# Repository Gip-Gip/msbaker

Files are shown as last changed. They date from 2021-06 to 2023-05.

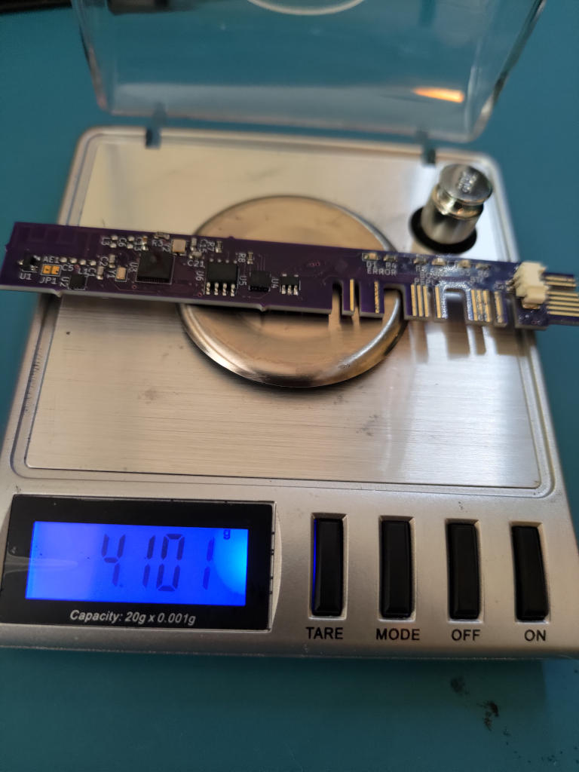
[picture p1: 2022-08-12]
docs/Images/msbaker_rev2_weight.jpg

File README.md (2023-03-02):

**Ms. Baker is a compact microcomputer built off the RP2040, specifically with model rocketry in mind.**
Occupying a footprint under 10cm&sup2;, this computer provides a unique density of many useful components, including a compact **25 pin GPIO** connector and a high accuracy **IMU**.
These features in a compact and light package is especially useful for low and medium power rockets, but may also find use in other applications where an ultra-small microcomputer may be needed.

## Feature Set

Ms. Baker is fairly feature packed for the size, and includes:

### RP2040 MCU

Powered by Raspberry Pi's RP2040 Microcontroller, Ms. Baker has the computation power of a 133MHz dual-core Arm Corted-M0+ processor in an unbelievably compact package.

### Micro SD Card Slot

Useful for logging data and loading/storing programs, Ms. Baker comes equipped with a compact MicroSD card slot for easy-to-use data storage.

### I2C IMU

No rocket computer should be complete with at least some form of telemetry, and Ms. Baker comes with the versitile LSM6DSO32 IMU, providing both gyro and acceleration data at a sample rate of up to 6.7kHz.
It has a maximum measurable acceleration range of &plusmn;32*g* and a maximum measurable angular rate of &plusmn;200dps, which should be good for most low and medium powered rockets, in theory.

### USB Programmable ROM

Thanks to the RP2040 Ms. Baker is entirely programmable via USB, meaning so long as you have a Micro USB cable and a computer you have access to **16MBytes of ROM** with no extra hardware!

### GPIO

Utilizing a Molex SlimStack connector Ms. Baker provides 25 pins of GPIO in a very compact footprint, completely up for any use the end user may desire!

### Robust Firmware

Like any other OpenApeShop project, Ms Baker's firmware is *(to be written)* in the Rust programming language, making it very robust and resistant to common bugs that may occur in other embedded firmware solutions.

## Development Status

**With a working prototype**, Ms. Baker is on it's third prototype and has the following steps that need to be completed before it is more or less ready for use:

- [ ] Program the firmware so that by default Ms. Baker acts as a telemetry logging device
- [ ] Field test Ms. Baker on a live rocket
- [ ] Reorganize PCB to fill up any unused space by
    - [ ] Spacing traces to reduce the chances of crosstalk, when possible
    - [ ] Increasing the size of traces to reduce impedence, when possible
- [ ] Document Ms. Baker so it's easy to use
- [ ] Develop a pin breakout board so prototyping is as easy as with a normal Raspberry Pi Pico

## Legal

Ms Baker's hardware is under the CERN-OHL-S and software under GPL-3.0.
See LEGAL-HARDWARE for all legal info regarding hardware, LEGAL-SOFTWARE for all legal info regarding software.

## Links

* [Website](https://openapeshop.org/hardware/msbaker)
* [Schematic](https://github.com/Gip-Gip/msbaker/raw/main/docs/Renders/schematic.png)

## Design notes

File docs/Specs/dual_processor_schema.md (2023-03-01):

---
title: "Dual Processor Schema"
date: 2023-03-01
author:
    - Charles Thompson
tags:
    - Specifications
    - Software
---
In embedded systems it is important that everything run efficiently as possible, and since the RP2040 is a dual core processor it would be a waste to not utilize both cores to their full potential. Therefore it is important to outline what responsibilities each core does so that programming for the processor is straightforward and well defined.

## Processor Responsibilities
Ms. Baker is to use a In-Out dual processor schema, in that one processor gathers input data and the other writes output data. The individual responsibilities are as follows:

### Core 0(In):
1. Initialize everything
2. Keep track of time
3. Read sensors on a consistent basis(be on time)
4. Handle aborts
5. Send data to core 0 to be processed, with high and low priority

### Core 1(Out):
1. Perform tasks assigned by core 0, high priority first, pertaining to
    * Computing and storing telemetry of the computer
    * Adjusting flight path and moving actuators when hooked up to external gear
    * Writing telemetry to the SD card

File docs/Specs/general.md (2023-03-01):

---
title: "General Specifications"
date: 2022-08-19
author:
    - Charles Thompson
tags:
    - Specifications
    - General
    - Overview
    - Hardware
    - Software
---
# General Specifications of the Ms. Baker Microcomputer
## The Need for a Compact Microcomputer in Rocketry

With modern advancements in chip design decreasing footprint and increasing computation power and effeciency, along with the shrinkage of many passive components, it is more than possible to cram fully capable flight computation units along with basic telemetry in a sub 10cm² package. The benefits for this are several, including but not limited to weight savings, dev time savings(not needing to design a custom computer for a project), and cost savings. This improvements are of both a combination of modern technology and advanced board design which is all open sourced and openly developed to help lead to future improvements in the unexplored tech. On top of that, these improvements are all fairly substantial to hobby model rocketry as every little change especially counts at the small rocket scale.

**Weight savings** is the primary benefit of the Ms. Baker microcomputer. The second iteration of the microcomputer only weighed in at **4g** in total, which is only really comparible to basic barometer altimeters and blows any proper flight computer out of the water[1]. Less weight leads to a higher acceleration under the same force, and consequentially a higher apogee aswell [2]. These weight savings are very significant as they can result in a multi-percent decrease in the total mass of a common 100-300g rocket[3]. For example, you replace a 15g flight computer on an 100g rocket(with a gross weight of 115g) with Ms. Baker which comes in at 4g(a new gross weight of 104g), you get a weight reduction of 9.6%, which is not insubstantial by any means.

**Development time** is saved by making Ms. Baker versitile and GPIO-ready. Most model rocket altimeters and flight computers are either massive and expensive, or have little to no expandable GPIO[1]. Ms. Baker aims to fill a niche by providing **I2C GPIO** to the end user so they can implement pyro controls, flight controls, and etc. themselves without having to worry about developing the complex circuitry to support a **full 32-bit microcontroller**. This also allows for **easier and more robust programming** as even simple solutions can utilize a 32-bit ARM core to speed up and improve accuracy for any need that may be. Even larger projects can utilize Ms. Baker as the brains for their custom boards as it's small footprint allows for more space for power electronics and other chips & sensors that may be needed.

**Cost Savings** *todo*

## What is Required for Ms. Baker to Meet It's Goals?

Ms. Baker has a lot of things it needs to fullfill, and each requirement brings it twords the goal of it being a fully fledged microcomputer

 * A **RP2004** MCU at the heart of the project. The RP2040 is low cost and OSH-friendly, with an open-source bootROM and good support for Rust
 * Firmware programmed in **Rust**. Rust is a powerful language that enforces good programming habits and allows the firmware to be far more robust by nature than if it were built in another language such as C or C++
 * On-board **accelerometer** and **gyroscope**, ideally in the same chip as this allows Ms. Baker to keep approximate relative location of the microcomputer
 * **10 meter** apogee accuracy when measuring apogee, under 10000 meters
 * Robust **GPIO** connectors and/or headers for expanding the use of the computer into other projects, with a minimum of one **I2C** interface
 * **USB** interface for extracting data from previous flights *and* programming the computer
 * **4MB** flash storage for plenty of room to program
 * **F-RAM** for storing non-volitile flight telemetry data
 * Total area under **10cm²**, and ideally small enough to fit into an estes gnome

## Finding Telemetric Accuracy
### Calculating Distance from Rocket Acceleration

First you need to find the initial hypothetical apogee from a hypothetical rocket's acceleration. Let's say the rocket accelerates at around 16g for 1 second, the rocket would gain $s_1$ distance and $v_1$ velocity by the time the rocket looses power
  $$
  \begin{aligned}
  &v = u + at\\
  &v = 0 + 156.9_{m/s^2}\cdot1_s\\
  \\
  &v_1 = 156.9_{m/s}
  \end{aligned}
 $$
$$
\begin{aligned}
\\
&v^2=u^2+2as\\
&2as=v^2-u^2\\
&s_1=\frac{v_1^2-u^2}{2a}\\
\\
&s_1=\frac{156.9_{m/s}^2-0_{m/s}^2}{2\cdot156.9_{m/s^2}}
\\
&s_1=78.5_m
\end{aligned}
$$
Then from there you can find the distance($s_2$) it takes the rocket to reach it's apogee
$$
\begin{aligned}
&u_2=v_1\\
\\
&s_2=\frac{v_2^2-u_2^2}{2a_2}\\
\\
&s_2=\frac{0_{m/s}^2-156.9_{m/s}^2}{2\cdot-9.8_{m/s^2}}
\\
&s_2=1256_m
\end{aligned}
$$
After that, you can find the total distance($s_t$) by adding $s_1$ and $s_2$, in this case $s_t=s_1+s_2=1334.5_m$. To condense the steps needed to get $s_t$, we can simply concatenate the above math into one equation
$$
\begin{aligned}
&s_t = s_1 + s_2\\
&s_t = \frac{v_1^2}{2a}+\frac{-v_1^2}{2\cdot-9.8_{m/s^2}}\\
\\
&s_t = \frac{(at)^2}{2a}+\frac{(at)^2}{19.6_{m/s^2}}
\end{aligned}
$$

## Part Selection

 * MPU: **RP2040**
     * Open-Source boot rom
     * Flash-able without any extra hardware via USB
     * Micro-SD card support
     * 2 i2c interfaces, 2spi interfaces
     * Up to 16mb external programmable flash
 * IMU: **LSM6DSO32TR**
 * Flash: **W25Q128JVSIM TR**
     * Reccomended flash for the RP2040
     * 16mb fast program storage
 * Voltage Regulator: **MIC5365-3.3YC5-TR**
 * Micro-USB port: **105017-0001**
 * MicroSD card connector: **104031-0811**
 * GPIO connector: **5055513420**
 * Crystal: **445I23D12M00000**

# Citations

 1. “Model Rocket Altimeters: Comparison Guide,” *Model rocket altimeters: Comparison guide*. \[Online\]. Available: [http://rocketsetc.com/altimeter-comparison/](http://rocketsetc.com/altimeter-comparison/). \[Accessed: 12-Aug-2022\].
 2. T. Benson, “Acceleration during powered flight,” *NASA*, 15-Aug-1999. \[Online\]. Available: [https://www.grc.nasa.gov/www/k-12/VirtualAero/BottleRocket/airplane/rktapow.html](https://www.grc.nasa.gov/www/k-12/VirtualAero/BottleRocket/airplane/rktapow.html). \[Accessed: 12-Aug-2022\].
 3. “HB:modelrockets,” *LUNAR*. \[Online\]. Available: [http://www.lunar.org/wiki/tiki-index.php?page=HB%3AModelRockets](http://www.lunar.org/wiki/tiki-index.php?page=HB%3AModelRockets). \[Accessed: 12-Aug-2022\].

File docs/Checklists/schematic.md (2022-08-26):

---
title: "Schematic Checklist"
date: 2022-08-26
author:
    - Charles Thompson
tags:
    - Checklist
    - General
    - Hardware
---
# RP2040 Checklist
### Derived from [Hardware design with RP2040](https://datasheets.raspberrypi.com/rp2040/hardware-design-with-rp2040.pdf) and the RP2040 [Datasheet](https://datasheets.raspberrypi.com/rp2040/rp2040-datasheet.pdf)
 - [ ] Power
     - [ ] 3.3v LDO Voltage Regulator
     - [ ] Decoupling capacitors
         - [ ] 100n capacitors on pins 49, 42, 33, 22, 10, 1, 48 and 43
         - [ ] 100n capacitors on pins 50 and 23
         - [ ] 1u capacitors on pins 45 and 44
 - [ ] Flash Storage
     - [ ] W25Q128JVS flash chip
 - [ ] Crystal Oscillator
     - [ ] 33p capacitor connected to each pin on the crystal
     - [ ] 1k resister in series between the crystal and XOUT
     - [ ] Crystal with ESR of 50ohms and 18p load capacitance
 - [ ] I/O
     - [ ] USB
         - [ ] 27.4ohm resistor in series with USB_D+ and USB_D-
     - [ ] GPIO
         - [ ] All GPIO pins availible to the GPIO header, excluding GPIOs used for the SD card
         - [ ] Run, SWD, and SWCLK also availible to the GPIO header
     - [ ] I2C
         - [ ] Pullup resistors correct value
         - [ ] All ICs connected to I2C0 on pins 8 and 9
             - [ ] SDA on pin 8
             - [ ] SCL on pin 9
     - [ ] SD Card
         - [ ] 10u decoupling capacitor between VDD and ground
         - [ ] All data lines contiguous and in order
     - [ ] Green Status LED
         - [ ] 470 ohm current limiting resistor
     - [ ] Reset Header
         - [ ] Connected to the RUN pin
     - [ ] Bootsel Jumper
         - [ ] Connected to QSPI_SS
         - [ ] 1k resistor between jumper and ground
     - [ ] Test Pads
         - [ ] 3.3v test pad
         - [ ] 1.1v test pad
         - [ ] XIN test pad
         - [ ] I2C SDA test pad
         - [ ] I2C SCL test pad

# LSM6DSO32 Checklist
### Derived from [iNEMO inertial module: always-on 3D Accelerometer and 3D gyroscope](https://www.st.com/resource/en/datasheet/lsm6dso32.pdf)
 - [ ] Power
     - [ ] 3.3v supply connected to pins 8 and 5
     - [ ] 100n capacitors connected to pins 8 and 5
     - [ ] Ground connected to pins 6 and 7
 - [ ] I2C
     - [ ] SA0(pin 1) connected to ground to set the I2C lsbit to zero
     - [ ] SDx and SCx connected to ground
     - [ ] INT1 not connected
     - [ ] INT2 not connected
     - [ ] CS connected to 3.3v
     - [ ] SCL connected to I2C0_SCL
     - [ ] SDA connected to I2C0_SDA

# W25Q128JVSIM Checklist
### Derived from the W25Q128JV [Datasheet](https://www.winbond.com/hq/support/documentation/downloadV2022.jsp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) and [Hardware design with RP2040](https://datasheets.raspberrypi.com/rp2040/hardware-design-with-rp2040.pdf)
 - [ ] Power
     - [ ] 3.3v supply connected to pin 8
     - [ ] 100n capacitor connected to pin 8
     - [ ] Ground connected to pin 4
 - [ ] QSPI
     - [ ] QSPI_SS connected to CS
     - [ ] QSPI_SCLK connected to CLK
     - [ ] QSPI_SD0-3 connected to IO0-3

# MIC5365-3.3YC5 Checklist
### Derived from the MIC5465 [Datasheet](https://ww1.microchip.com/downloads/aemDocuments/documents/OTH/ProductDocuments/DataSheets/mic5365.pdf)
 - [ ] Power
     - [ ] 1u capacitor connected to both pins 1 and 5
     - [ ] VIN connected to +5v rail
     - [ ] VOUT connected to +3.3v rail
 - [ ] EN pin connected to +5v

# Final Checklist
 - [ ] RP2040 Checklist Complete
 - [ ] LSM6DSO32 Checklist Complete
 - [ ] W25Q128JVSIM Checklist Complete
 - [ ] MIC5365-3.3YC5 Checklist Complete
 - [ ] No unconnected pins or nets
 - [ ] ERC ran
 - [ ] Schematic organized
 - [ ] BOM generated
 - [ ] Footprints set
 - [ ] MPNs set

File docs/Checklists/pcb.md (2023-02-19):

---
title: "PCB Checklist"
date: 2022-08-26
author:
    - Charles Thompson
tags:
    - Checklist
    - General
    - Hardware
---
# RP2040 Checklist
### Derived from [Hardware design with RP2040](https://datasheets.raspberrypi.com/rp2040/hardware-design-with-rp2040.pdf) and the RP2040 [Datasheet](https://datasheets.raspberrypi.com/rp2040/rp2040-datasheet.pdf)
 - [ ] Power
     - [ ] Decoupling capacitors close to pins
 - [ ] Crystal Oscillator
     - [ ] Close to RP2040 to reduce parasitic capacitance
     - [ ] Capacitors and resistor close to crystal
 - [ ] Flash
     - [ ] Data lines short and close to the RP2040
 - [ ] I/O
     - [ ] USB
         - [ ] 0.8mm wide tracks spaced 0.15mm apart from R5 and R6

# LSM6DSO32 Checklist
### Derived from [iNEMO inertial module: always-on 3D Accelerometer and 3D gyroscope](https://www.st.com/resource/en/datasheet/lsm6dso32.pdf)
 - [ ] Power
     - [ ] Decoupling capacitors close to pins

# W25Q128JVSIM Checklist
### Derived from the W25Q128JV [Datasheet](https://www.winbond.com/hq/support/documentation/downloadV2022.jsp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) and [Hardware design with RP2040](https://datasheets.raspberrypi.com/rp2040/hardware-design-with-rp2040.pdf)
 - [ ] Power
     - [ ] Decoupling capacitors close to pins

# MIC5365-3.3YC5 Checklist
### Derived from the MIC5465 [Datasheet](https://ww1.microchip.com/downloads/aemDocuments/documents/OTH/ProductDocuments/DataSheets/mic5365.pdf)
 - [ ] Power
     - [ ] Decoupling capacitors close to pins

# Final Checklist
 - [ ] RP2040 Checklist Complete
 - [ ] LSM6DSO32 Checklist Complete
 - [ ] W25Q128JVSIM Checklist Complete
 - [ ] MIC5365-3.3YC5 Checklist Complete
 - [ ] No unconnected pins or nets
 - [ ] DRC ran

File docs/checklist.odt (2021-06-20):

Ms. Baker Schematic Checklist

Schematic Revision 2.3

Write component ids under the bullet point, if applicable

# ESP32 BLOCK

- 100nF capacitors connecting esp32/pins 19 and 37 respectively to ground
- esp32/pins 19 and 37 connected to V3.3+
- 1uF capacitor connecting esp32/pin 26 to ground
- 100nF, 1uF, and 10uF capacitors connecting both esp32/pins 3 and 4 to ground
- 2nH inductor connecting both esp32/pins 3 and 4 to the aformentioned bypass capacitors
- both esp32/pins 3 and 4 connected to V3.3+
- 100pF and 1uF capacitors connecting both esp32/pins 46 and 43 to ground
- both esp32/pins 46 and 43 connected to V3.3+
- 100nF capacitor connecting esp32/pin 1 to ground
- esp32/pin 1 connected to V3.3+
- esp32/pin 9 connected to reset
- 10nF capacitor connecting esp32/pin48 to ground
- 499ohm resistor connecting esp32/pin 41 to UART_TX
- esp32/pin 25 connected to SPI_CS
- esp32/pin 27 connected to SPI_IO1
- esp32/pin 30 connected to SPI_IO3
- esp32/pin 31 connected to SPI_CLK
- esp32/pin 32 connected to SPI_IO2
- esp32/pin 33 connected to SPI_IO0
- esp32/pin 14 connected to I2C_SCK
- esp32/pin 15 connected to I2C_SDA
- esp32/pin 23 connected to BOOTMODE
- esp32/pin 40 connected to UART_RX
- esp32/pin 34 connected to the BT STATUS LED
- esp32/pin 35 connected to the BOOT STATUS LED
- esp32/pin 36 connected to the ERROR LED
- esp32/pin 17 connected to JTAG_MTMS
- esp32/pin 18 connected to JTAG_MTDI
- esp32/pin 20 connected to JTAG_MTCK
- esp32/pin 21 connected to JTAG_MTDO

# CPU CRYSTAL BLOCK

- 40MHz crystal connected between esp32/pins 44 and 45
- 0ohm resistor in series between esp32/pin 45 and the 40MHz crystal
- 12pF capacitors connected to both 40MHz/pins 1 and 3 respectively
- 40MHz/pins 2 and 4 connected to ground

# RTC CRYSTAL BLOCK

- 32.768kHz crystal connected between esp32/pins 12 and 13
- 12pF capacitors connected to both 32.768kHz/pins 1 and 2 respectively

# RESET BLOCK

- 100nF capacitor connecting mcp130/pin 2 to ground
- jumper connecting mcp130/pin1 to reset
- mcp130/pin 2 connected to V3.3+
- mcp130/pin 3 connected to ground

# ANTENNA BLOCK

- One inductor and two capacitors configured in pi-style matching network
- Use center-tapped inductor or two inductors for tuning

# I2C PULLUP BLOCK

- 2 12kOhm resistors connecting I2C_SCK and I2C_SDA respectively to V3.3+

# LED BLOCK

- 120Ohm resistor between each LED and their respective esp32 pin
- 2.1v LEDs
- BLUE=BLUETOOTH, GREEN=STATUS, RED=ERROR

# POWER SUPPLY BLOCK

- 10uF capacitor connecting adp124/pins 7 and 8 to ground
- 10uF capacitor connecting adp124/pins 1 and 2 to ground
- 1uF capacitor connecting adp150/pin 1 to ground
- 1uF capacitor connecting adp150/pin 5 to ground
- adp124/pins 5, 7 and 8 connected to a 3.7v LiPo battery, preferably via a Molex Picoblade
- adp124/pins 1, 2, and 3 connected to V3.3+
- adp124/pin 4 connected to ground
- adp150/pins 1 and 3 connected to V3.3+
- adp150/pin 2 connected to ground
- adp150/pin 5 connected to V1.8+

# IMU BLOCK

- 100nF and 2.2uF capacitor connecting icm20601/pin 16 to ground
- 10nF capacitor connecting icm20601/pin 1 to ground
- 470nF capacitor connecting icm20601/pin 14 to ground
- icm20601/pin 1 connected to V3.3+
- icm20601/pin 2 connected to I2C_SCK
- icm20601/pin 3 connected to I2C_SDA
- icm20601/pin 4 connected to ground
- icm20601/pin 5 connected to V3.3+
- icm20601/pin 8 connected to ground
- icm20601/pin 13 connected to ground
- icm20601/pin 16 connected to V1.8V+

# FERAM BLOCK

- 2.2uF capacitor connecting fm24v01/pin 8 to ground
- fm24v01/pins 1, 2, and 3 connected to ground
- fm24v01/pin 4 connected to ground
- fm24v01/pin 5 connected to I2C_SDA
- fm24v01/pin 6 connected to I2C_SCK
- fm24v01/pin 7 connected to ground
- fm24v01/pin 8 connected to V3.3+

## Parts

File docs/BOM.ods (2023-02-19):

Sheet: product
References | Value | Footprint | Cost | MPN | Quantity | Supplier | Total Cost
C2 | 10u | Capacitor_SMD:C_0603_1608Metric | 0.38 | C1608X5R0J106K080AE | 1 | Digi-Key | 0.38
C1, C3, C7, C20 | 1u | Capacitor_SMD:C_0402_1005Metric | 0.19 | C1005X5R1E105K050BE | 4 | Digi-Key | 0.76
C4, C5 | 33p | Capacitor_SMD:C_0402_1005Metric | 0.1 | CGA2B2C0G1H330J050BA | 2 | Digi-Key | 0.2
C6, C8-C19 | 100n | Capacitor_SMD:C_0402_1005Metric | 0.2 | C1005X7R1H104K050BE | 13 | Digi-Key | 2.6
D1 | 2.1v | LED_SMD:LED_0402_1005Metric | 0.38 | APHHS1005CGCK | 1 | Digi-Key | 0.38
J1 | USB_B_Micro | Connector_USB:USB_Micro-B_Molex-105017-0001 | 0.96 | 105017-0001 | 1 | Digi-Key | 0.96
J2 | Micro_SD_Card | Connector_Card:microSD_HC_Molex_104031-0811 | 2.22 | 104031-0811 | 1 | Digi-Key | 2.22
J3 | GPIO | msbaker:5055513420 | 1.57 | 505551-3420 | 1 | Digi-Key | 1.57
JP1, JP2 | BOOTSEL, RESET | Connector_PinHeader_2.54mm:PinHeader_1x02_P2.54mm_Vertical |  |  | 2 | Digi-Key
R1, R2 | 15k | Resistor_SMD:R_0402_1005Metric | 0.1 | AC0402FR-0715KL | 2 | Digi-Key | 0.2
R3, R4 | 1k | Resistor_SMD:R_0402_1005Metric | 0.1 | AC0402FR-071KL | 2 | Digi-Key | 0.2
R5, R6 | 27.4 | Resistor_SMD:R_0402_1005Metric | 0.1 | AC0402FR-0727R4L | 2 | Digi-Key | 0.2
R7 | 470 | Resistor_SMD:R_0402_1005Metric | 0.1 | AC0402FR-07470RL | 1 | Digi-Key | 0.1
U1 | MIC5365-3.3YC5 | Package_TO_SOT_SMD:SOT-353_SC-70-5 | 0.19 | MIC5365-3.3YC5-TR | 1 | Digi-Key | 0.19
U2 | W25Q128JVS | Package_SO:SOIC-8_5.23x5.23mm_P1.27mm | 1.95 | W25Q128JVSIM TR | 1 | Digi-Key | 1.95
U3 | RP2040 | RP2040_minimal:RP2040-QFN-56 | 1 | RP2040TR13 | 1 | Digi-Key | 1
U4 | LSM6DSO32 | Package_LGA:LGA-14_3x2.5mm_P0.5mm_LayoutBorder3x4y | 5.47 | LSM6DSO32TR | 1 | Digi-Key | 5.47
Y1 | 12MHz | Crystal:Crystal_SMD_5032-2Pin_5.0x3.2mm | 0.76 | 445I23D12M00000 | 1 | Digi-Key | 0.76
PCB | 4 Layer | - | 4.47 | - | 1 | OSH Park | 4.47
 |  |  |  |  |  |  | Cost per unit
 |  |  |  |  |  |  | 23.61

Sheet: operations
Description | Cost | MPN | Quantity | Supplier | Total Cost
Stencils | 24.7 | - | 1 | OSH Stencis | 24.7

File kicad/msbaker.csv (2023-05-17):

Source: | /home/thompsonc/Projects/msbaker/kicad/msbaker.kicad_sch
Date: | Wed 17 May 2023 01:07:28 PM EDT
Tool: | Eeschema 7.0.1
Generator: | /usr/share/kicad/plugins/bom_csv_grouped_by_value.py
Component Count: | 39
Collated Components:
Item | Qty | Reference(s) | Value | LibPart | Footprint | Datasheet | DNP | Cost | MPN | Note
1 | 2 | C1, C3 | 1u | Device:C | Capacitor_SMD:C_0402_1005Metric | ~ |  | 0.19 | C1005X5R1E105K050BE
2 | 2 | C2, C21 | 4.7u | Device:C | Capacitor_SMD:C_0402_1005Metric | ~ |  | 0.53 | C1005X5R1A475K050BE
3 | 2 | C4, C5 | 33p | Device:C_Small | Capacitor_SMD:C_0402_1005Metric | ~ |  | 0.1 | CGA2B2C0G1H330J050BA
4 | 13 | C6, C8, C9, C10, C11, C12, C13, C14, C15, C16, C17, C18, C19 | 100n | Device:C_Small | Capacitor_SMD:C_0402_1005Metric | ~ |  | 0.2 | C1005X7R1H104K050BE
5 | 2 | C7, C20 | 1u | Device:C_Small | Capacitor_SMD:C_0402_1005Metric | ~ |  | 0.19 | C1005X5R1E105K050BE
6 | 1 | D1 | 2.1v | Device:LED | LED_SMD:LED_0402_1005Metric | ~ |  | 0.37 | APHHS1005CGCK
7 | 1 | J1 | USB_B_Micro | Connector:USB_B_Micro | Connector_USB:USB_Micro-B_Molex-105017-0001 | ~ |  | 0.96 | 105017-0001
8 | 1 | J2 | Micro_SD_Card | Connector:Micro_SD_Card | Connector_Card:microSD_HC_Molex_104031-0811 | http://katalog.we-online.de/em/datasheet/693072010801.pdf |  | 2.22 | 104031-0811
9 | 1 | J3 | GPIO | Connector_Generic:Conn_02x17_Odd_Even | msbaker:5055513420 | ~ |  | 1.57 | 505551-3420
12 | 2 | R3, R4 | 1k | Device:R_Small | Resistor_SMD:R_0402_1005Metric | ~ |  | 0.1 | AC0402FR-071KL
13 | 2 | R5, R6 | 27.4 | Device:R_Small | Resistor_SMD:R_0402_1005Metric | ~ |  | 0.1 | AC0402FR-0727R4L
14 | 1 | R7 | 470 | Device:R_Small | Resistor_SMD:R_0402_1005Metric | ~ |  | 0.1 | AC0402FR-07120RL
17 | 1 | U1 | MIC5365-3.3YC5 | Regulator_Linear:MIC5365-3.3YC5 | Package_TO_SOT_SMD:SOT-353_SC-70-5 | http://ww1.microchip.com/downloads/en/DeviceDoc/mic5365.pdf |  | 0.19 | MIC5365-3.3YC5-TR
18 | 1 | U2 | W25Q128JVS | Memory_Flash:W25Q128JVS | Package_SO:SOIC-8_5.23x5.23mm_P1.27mm | http://www.winbond.com/resource-files/w25q128jv_dtr%20revc%2003272018%20plus.pdf |  | 1.95 | W25Q128JVSIM TR
19 | 1 | U3 | RP2040 | msbaker:RP2040 | msbaker:RP2040-QFN-56 |  |  | 1 | RP2040TR13
20 | 1 | U4 | LSM6DSO32 | Sensor_Motion:LSM6DS3 | Package_LGA:LGA-14_3x2.5mm_P0.5mm_LayoutBorder3x4y | www.st.com/resource/en/datasheet/lsm6ds3.pdf |  | 5.47 | LSM6DSO32TR | Derived from LSM6DS3 footprint, identical pinout
21 | 1 | Y1 | 12MHz | Device:Crystal_Small | Crystal:Crystal_SMD_5032-2Pin_5.0x3.2mm | ~ |  | 0.76 | 445I23D12M00000

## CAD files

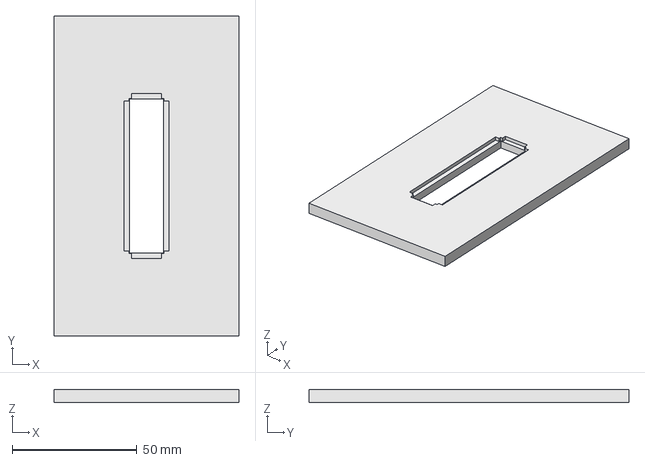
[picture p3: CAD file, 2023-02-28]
freecad/solderjig.FCStd
74.0 x 128.0 x 5.00 mm

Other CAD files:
freecad/solderjig.3mf

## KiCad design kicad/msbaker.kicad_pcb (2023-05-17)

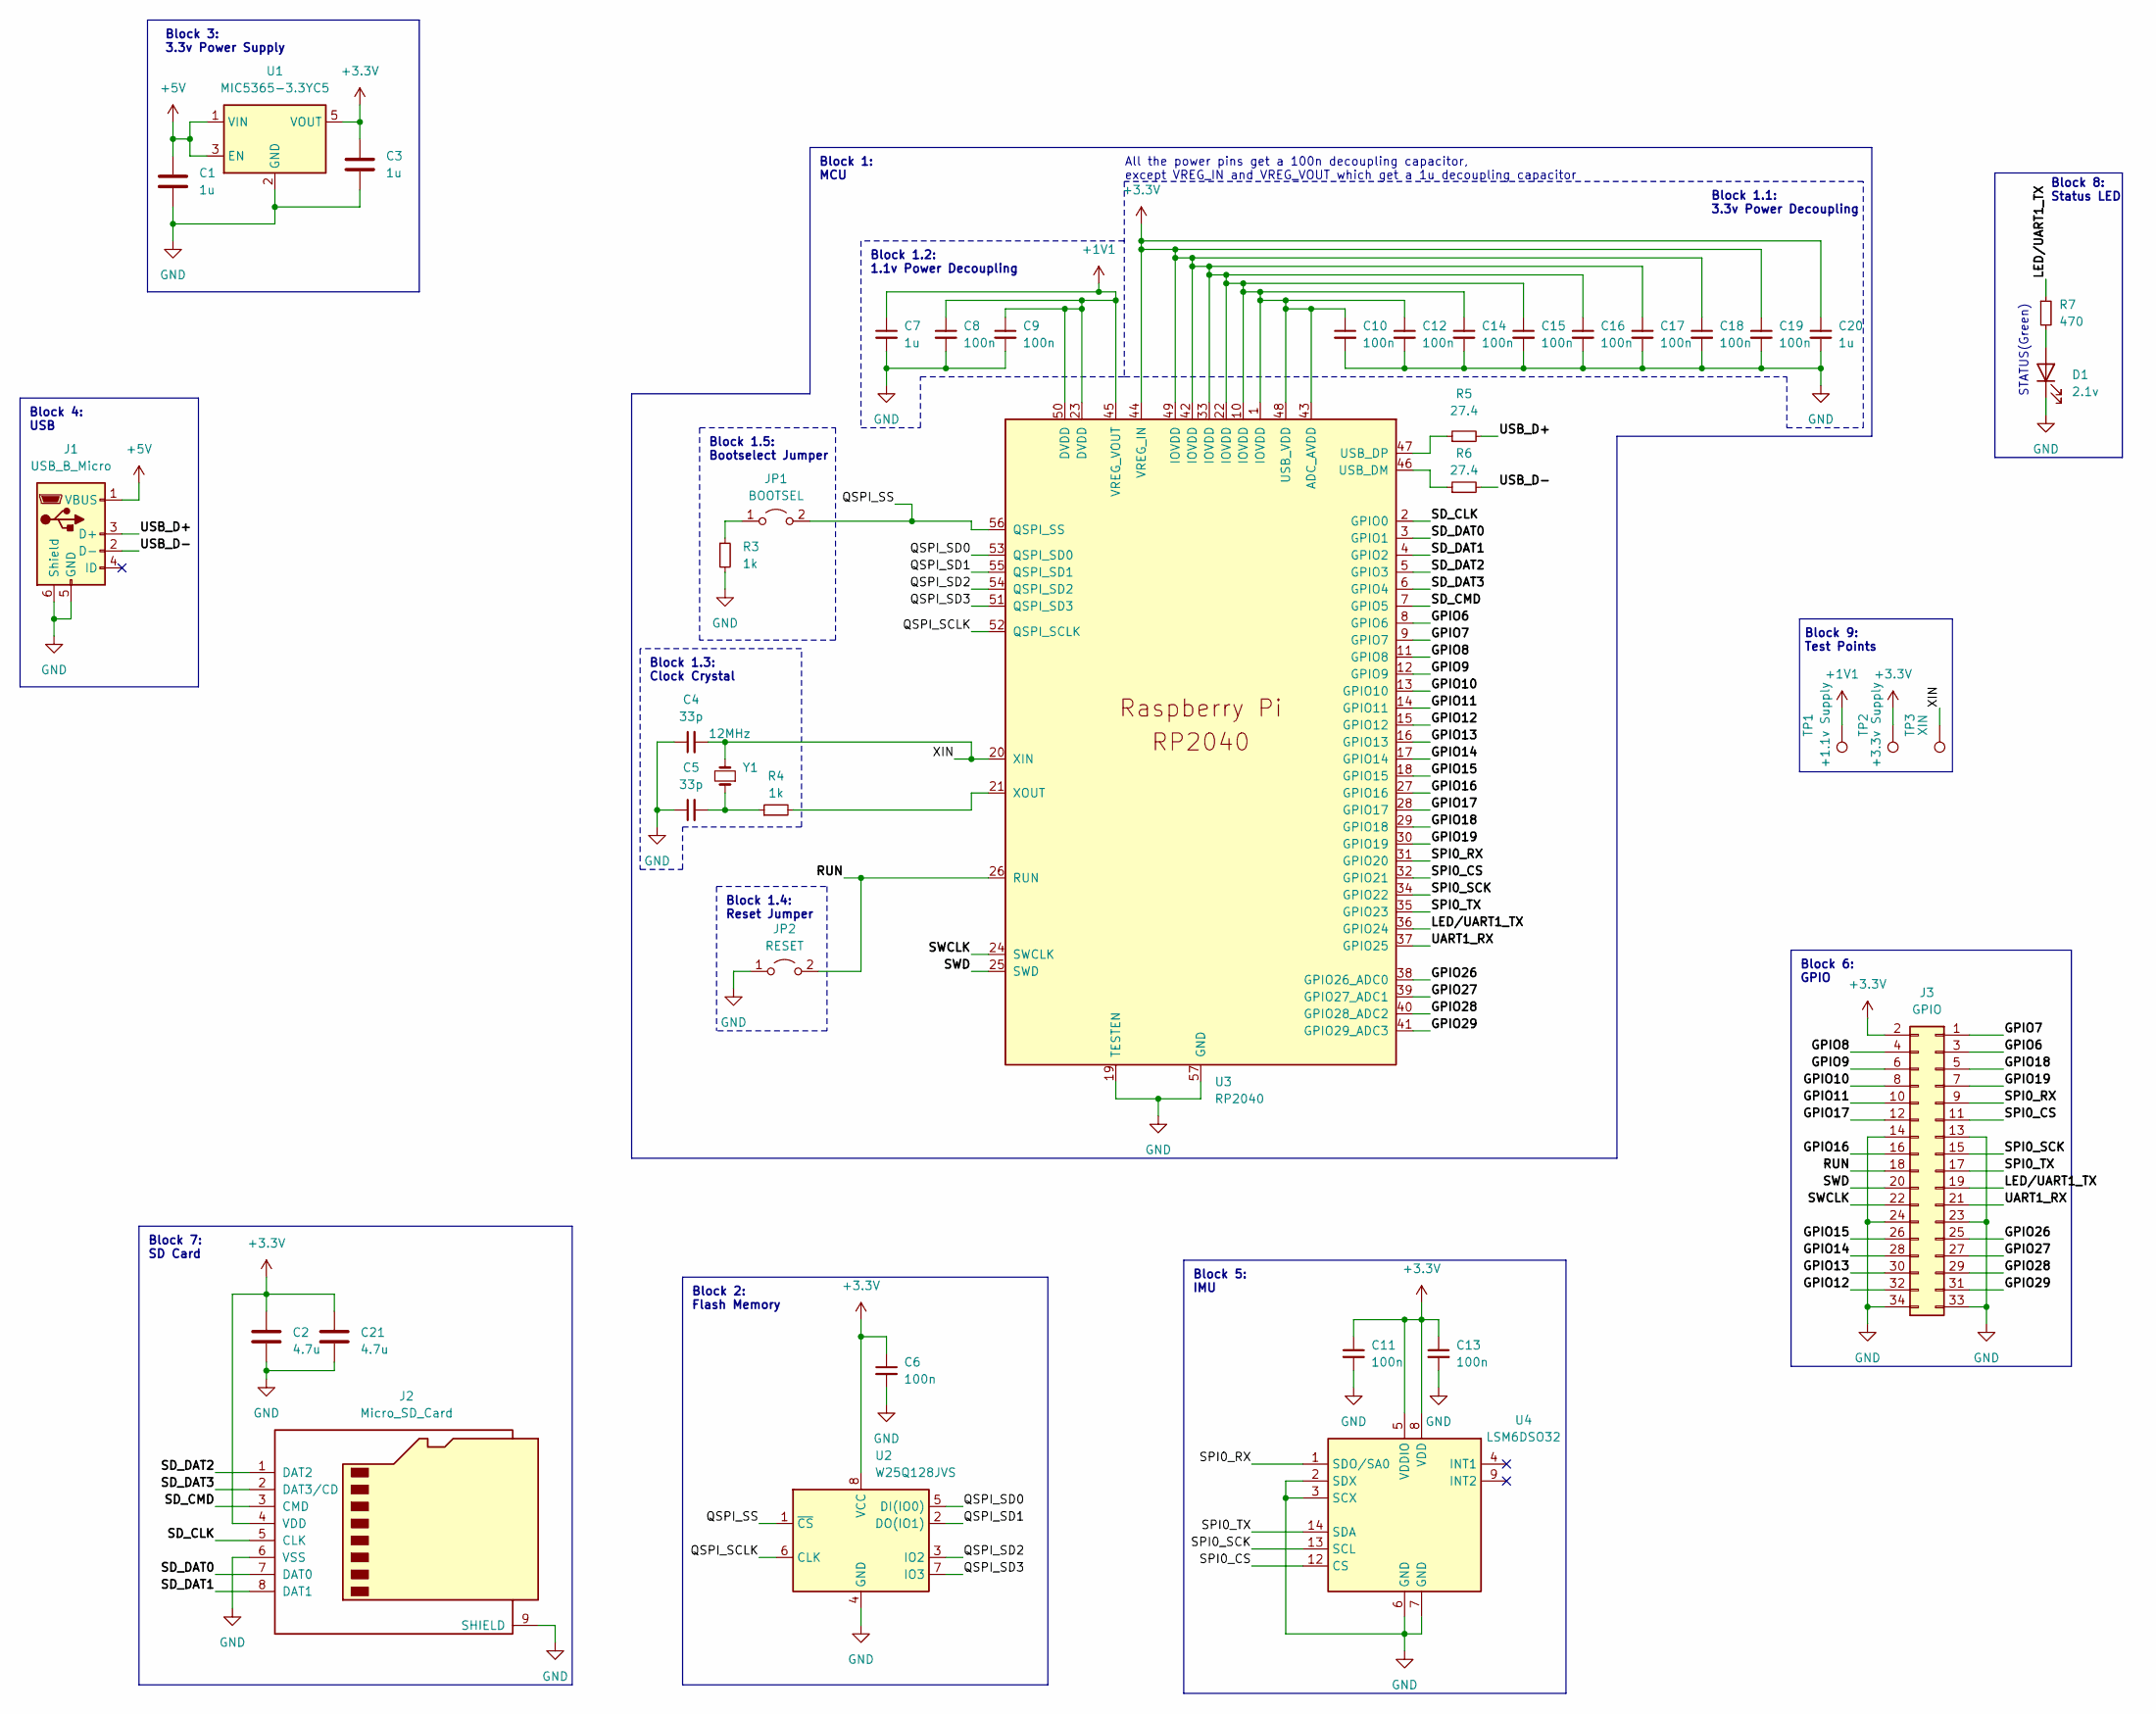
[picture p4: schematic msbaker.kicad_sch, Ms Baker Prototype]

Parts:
C1, C3, C7, C20: 1u; C_0402_1005Metric; MPN C1005X5R1E105K050BE
C2, C21: 4.7u; C_0402_1005Metric; MPN C1005X5R1A475K050BE
C4, C5: 33p; C_0402_1005Metric; MPN CGA2B2C0G1H330J050BA
C6, C8, C9, C10, C11, C12, C13, C14, C15, C16, C17, C18, C19: 100n; C_0402_1005Metric; MPN C1005X7R1H104K050BE
D1: 2.1v; LED_0402_1005Metric; MPN APHHS1005CGCK
J1: USB_B_Micro; USB_Micro-B_Molex-105017-0001; MPN 105017-0001
J2: Micro_SD_Card; microSD_HC_Molex_104031-0811; MPN 104031-0811
J3: GPIO; 5055513420; MPN 505551-3420
JP1: BOOTSEL; poke_jumper
JP2: RESET; poke_jumper
R3, R4: 1k; R_0402_1005Metric; MPN AC0402FR-071KL
R5, R6: 27.4; R_0402_1005Metric; MPN AC0402FR-0727R4L
R7: 470; R_0402_1005Metric; MPN AC0402FR-07120RL
TP1: +1.1v Supply; TestPoint_Pad_1.0x1.0mm
TP2: +3.3v Supply; TestPoint_Pad_1.0x1.0mm
TP3: XIN; TestPoint_Pad_1.0x1.0mm
U1: MIC5365-3.3YC5; SOT-353_SC-70-5; MPN MIC5365-3.3YC5-TR
U2: W25Q128JVS; SOIC-8_5.23x5.23mm_P1.27mm; MPN W25Q128JVSIM TR
U3: RP2040; RP2040-QFN-56; MPN RP2040TR13
U4: LSM6DSO32; LGA-14_3x2.5mm_P0.5mm_LayoutBorder3x4y; MPN LSM6DSO32TR
Y1: 12MHz; Crystal_SMD_5032-2Pin_5.0x3.2mm; MPN 445I23D12M00000

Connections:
+1V1: C7.1, C8.1, C9.1, TP1.1, U3.23 (DVDD), U3.45 (VREG_VOUT), U3.50 (DVDD)
+3.3V: C2.1, C3.1, C6.1, C10.1, C11.1, C12.1, C13.1, C14.1, C15.1, C16.1, C17.1, C18.1, C19.1, C20.1, C21.1, J2.4 (VDD), J3.2, TP2.1, U1.5 (VOUT), U2.8 (VCC), U3.1 (IOVDD), U3.10 (IOVDD), U3.22 (IOVDD), U3.33 (IOVDD), U3.42 (IOVDD), U3.43 (ADC_AVDD), U3.44 (VREG_IN), U3.48 (USB_VDD), U3.49 (IOVDD), U4.5 (VDDIO), U4.8 (VDD)
+5V: C1.1, J1.1 (VBUS), U1.1 (VIN), U1.3 (EN)
/GPIO6: J3.3, U3.8 (GPIO6)
/GPIO7: J3.1, U3.9 (GPIO7)
/GPIO8: J3.4, U3.11 (GPIO8)
/GPIO9: J3.6, U3.12 (GPIO9)
/GPIO10: J3.8, U3.13 (GPIO10)
/GPIO11: J3.10, U3.14 (GPIO11)
/GPIO12: J3.32, U3.15 (GPIO12)
/GPIO13: J3.30, U3.16 (GPIO13)
/GPIO14: J3.28, U3.17 (GPIO14)
/GPIO15: J3.26, U3.18 (GPIO15)
/GPIO16: J3.16, U3.27 (GPIO16)
/GPIO17: J3.12, U3.28 (GPIO17)
/GPIO18: J3.5, U3.29 (GPIO18)
/GPIO19: J3.7, U3.30 (GPIO19)
/GPIO26: J3.25, U3.38 (GPIO26_ADC0)
/GPIO27: J3.27, U3.39 (GPIO27_ADC1)
/GPIO28: J3.29, U3.40 (GPIO28_ADC2)
/GPIO29: J3.31, U3.41 (GPIO29_ADC3)
/LED/UART1_TX: J3.19, R7.1, U3.36 (GPIO24)
/QSPI_SCLK: U2.6 (CLK), U3.52 (QSPI_SCLK)
/QSPI_SD0: U2.5 (DI(IO0)), U3.53 (QSPI_SD0)
/QSPI_SD1: U2.2 (DO(IO1)), U3.55 (QSPI_SD1)
/QSPI_SD2: U2.3 (IO2), U3.54 (QSPI_SD2)
/QSPI_SD3: U2.7 (IO3), U3.51 (QSPI_SD3)
/QSPI_SS: JP1.2 (B), U2.1 (~CS), U3.56 (QSPI_SS); also elsewhere on the board
/RUN: J3.18, JP2.2 (B), U3.26 (RUN); also elsewhere on the board
/SD_CLK: J2.5 (CLK), U3.2 (GPIO0)
/SD_CMD: J2.3 (CMD), U3.7 (GPIO5)
/SD_DAT0: J2.7 (DAT0), U3.3 (GPIO1)
/SD_DAT1: J2.8 (DAT1), U3.4 (GPIO2)
/SD_DAT2: J2.1 (DAT2), U3.5 (GPIO3)
/SD_DAT3: J2.2 (DAT3/CD), U3.6 (GPIO4)
/SPI0_CS: J3.11, U3.32 (GPIO21), U4.12 (CS)
/SPI0_RX: J3.9, U3.31 (GPIO20), U4.1 (SDO/SA0)
/SPI0_SCK: J3.15, U3.34 (GPIO22), U4.13 (SCL)
/SPI0_TX: J3.17, U3.35 (GPIO23), U4.14 (SDA)
/SWCLK: J3.22, U3.24 (SWCLK)
/SWD: J3.20, U3.25 (SWD)
/UART1_RX: J3.21, U3.37 (GPIO25)
/USB_D+: J1.3 (D+), R5.2
/USB_D-: J1.2 (D-), R6.2
/XIN: C4.2, TP3.1, U3.20 (XIN), Y1.2
GND: C1.2, C2.2, C3.2, C4.1, C5.1, C6.2, C7.2, C8.2, C9.2, C10.2, C11.2, C12.2, C13.2, C14.2, C15.2, C16.2, C17.2, C18.2, C19.2, C20.2, C21.2, D1.1 (K), J1.5 (GND), J1.6 (Shield), J2.6 (VSS), J2.9 (SHIELD), J3.13, J3.14, J3.23, J3.24, J3.33, J3.34, J3.GND, JP2.1 (A), R3.2, U1.2 (GND), U2.4 (GND), U3.19 (TESTEN), U3.57 (GND), U4.2 (SDX), U4.3 (SCX), U4.6 (GND), U4.7 (GND); also elsewhere on the board
unnamed: C5.2, R4.1, Y1.1
unnamed: D1.2 (A), R7.2
unnamed 48: JP1.1 (A), R3.1; also elsewhere on the board
unnamed: R6.1, U3.46 (USB_DM)
unnamed: R5.1, U3.47 (USB_DP)
unnamed: R4.2, U3.21 (XOUT)

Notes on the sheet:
STATUS(Green)
Block 1: MCU
Block 5: IMU
Block 3: 3.3v Power Supply
Block 4: USB
Block 7: SD Card
Block 1.3: Clock Crystal
Block 1.5: Bootselect Jumper
Block 6: GPIO
Block 1.2: 1.1v Power Decoupling
Block 1.1: 3.3v Power Decoupling
All the power pins get a 100n decoupling capacitor, except VREG_IN and VREG_VOUT which get a 1u decoupling capacitor
Block 8: Status LED
Block 2: Flash Memory
Block 9: Test Points
Block 1.4: Reset Jumper

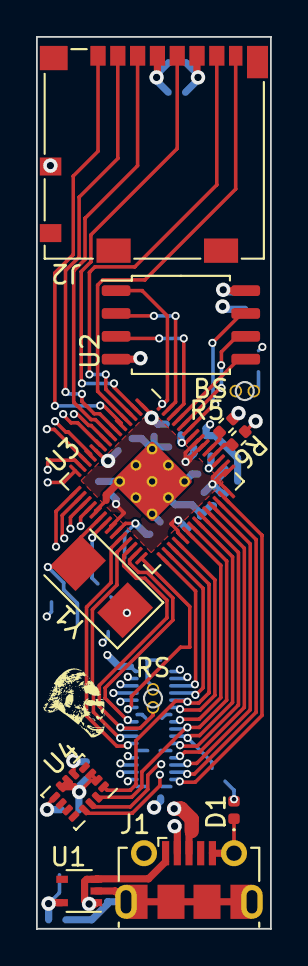
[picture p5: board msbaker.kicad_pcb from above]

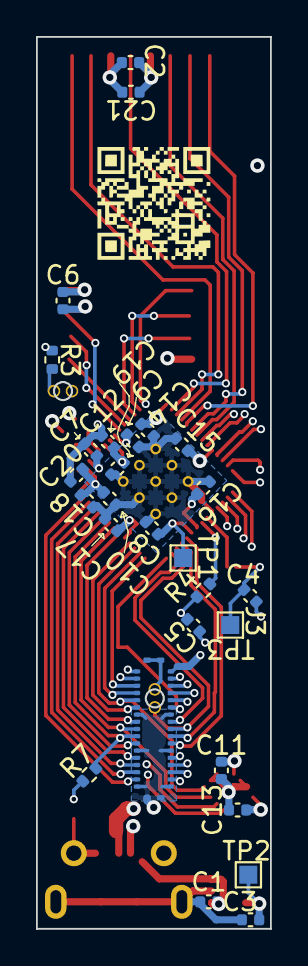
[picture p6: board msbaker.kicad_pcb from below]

Board: 4 copper layers, 13.0 x 49.5 mm, 40 parts (28 on the bottom side), 52 nets.

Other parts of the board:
BS: BOOTSEL; poke_jumper
RS: RESET; poke_jumper

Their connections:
/QSPI_SS: BS.2 (B); also elsewhere on the board
/RUN: RS.2 (B); also elsewhere on the board
GND: RS.1 (A); also elsewhere on the board
unnamed 48: BS.1 (A); also elsewhere on the board

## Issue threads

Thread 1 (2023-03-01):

Blink LED On Panic

Gip-Gip, 2023-03-01:
Since embedded rust requires it's own panic handler, it would be convenient to communicate the panic message through LED so that the end user can decipher what went wrong without needing specially JTAG or anything else. The message should be short and easy to decipher, perhaps through Morse code or something alike.

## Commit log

2021-01-11 Basic Arduino/Eclipse setup initialized
2021-01-21 Added circuit board and design docs
    [mbaker.kicad_pcb, mbaker.sch]
2021-01-21 Added PDF of current schematic
2021-01-27 Schematic completed, documentation in progress
    [mbaker.sch]
2021-02-19 Adjusted 3 wire UART and removed 3/4 the ram
    [mbaker.sch]
2021-03-30 Finished revision 1 schematic
    [mbaker.sch, refsheet.ods]
2021-04-16 Finalized prototype and prototype BOM
    [BOM.ods, mbaker.sch]
2021-05-05 Updated source code, currently untested
2021-05-12 Finished test UART program
2021-05-19 Total schematic redesign
    [BOM.ods, PCBEdgePinouts.ods, mbaker.sch]
2021-05-24 Rough draft of revision 2.1 schematic
    [PCBEdgePinouts.ods, mbaker.sch]
2021-06-20 Finalized 2.3.1 prototype
    [BOM.ods, PCBEdgePinouts.ods, mbaker.kicad_pcb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]
2021-07-20 Started revision 2.4.0
    [mbaker.kicad_pcb, mbaker.sch, pinouts.ods]
2021-07-20 Modified PCB edge connectors
    [mbaker.sch, pinouts.ods]
2021-08-16 Started work on the website and revision 2.4.0
    [mbaker-pcb.dxf]
2022-08-14 Completed RP2040 power decoupling circuitry
    [mbaker.kicad_pcb, mbaker.sch, msbaker.kicad_pcb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]
2022-08-14 Added clock crystal block
    [msbaker.kicad_sch]
2022-08-15 Added flash memory block
    [msbaker.kicad_sch]
2022-08-15 Added 3.3v power supply block
    [msbaker.kicad_sch]
2022-08-15 Added imu block
    [msbaker.kicad_sch]
2022-08-18 Added USB block
    [msbaker.kicad_sch]
2022-08-18 Added in-series resistors for the USB data lines
    [msbaker.kicad_sch]
2022-08-18 Added gpio block
    [msbaker.kicad_sch]
2022-08-18 Changed the layout of the schematic
    [msbaker.kicad_sch]
2022-08-19 Assigned footprints
    [msbaker.kicad_sch]
2022-08-19 Applied footprints + Added LED block + Created design checklist
    [msbaker.csv, msbaker.kicad_sch]
2022-08-19 Corrected small mistake where I2C0 was placed on GPIO8 and GPIO9 instead of chip pin 8 and 9
    [msbaker.kicad_sch]
2022-08-20 Created BOM
    [BOM.ods, bom.csv, msbaker.csv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]
2022-08-20 Corrected block numbers
    [msbaker.kicad_sch]
2022-08-20 Fixed typo in schematic
    [BOM.ods, msbaker.kicad_pcb, msbaker.kicad_sch]
2022-08-21 Added pcb files
    [msbaker.kicad_pcb, msbaker.kicad_sch]
2022-08-25 Fixed references on silkscreen layer
    [msbaker.kicad_pcb]
2022-08-25 Added reset jumper block
    [msbaker.kicad_sch]
2022-08-25 Separated the bootsel jumper into it's own block
    [msbaker.kicad_sch]
2022-08-25 Updated BOM
    [BOM.ods, msbaker.kicad_sch]
2022-08-25 Added reset jumper to PCB
    [msbaker.kicad_pcb]
2022-08-25 Fixed DRC violations
    [msbaker.kicad_pcb]
2022-08-25 Added M2 screw holes to the solder paste layer to give points to align the solder paste stencil
    [BOM.ods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]
2022-08-26 Changed status led resistor to 480 to improve efficiency
    [BOM.ods, msbaker.kicad_sch]
2022-08-26 Added test points to schematic
    [BOM.ods, msbaker.kicad_sch]
2022-08-26 Corrected typo on schematic
    [BOM.ods, msbaker.kicad_sch]
2023-02-19 Updated to v3
    [BOM.ods, bom.csv, msbaker.kicad_pcb]
2023-02-28 Created Hello World firmware
    [solderjig.3mf, solderjig.FCStd]
2023-03-01 Added dual core schema and removed old 2.3.1 files
    [mbaker-pcb.dxf, pinouts.ods]
2023-03-02 Added IMU self check
2023-05-17 Changed IMU to SPI and shrunk board
    [msbaker.csv, msbaker.kicad_pcb, msbaker.kicad_sch]
